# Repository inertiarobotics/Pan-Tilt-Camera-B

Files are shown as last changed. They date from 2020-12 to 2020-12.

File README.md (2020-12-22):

# Pan Tilt Mechanism - Version B
A lightweight and a less bulkier version of [Pan Tilt Camera A](https://github.com/inertiarobotics/Pan-Tilt-Camera-A)

For Raspberry Pi Camera V2.

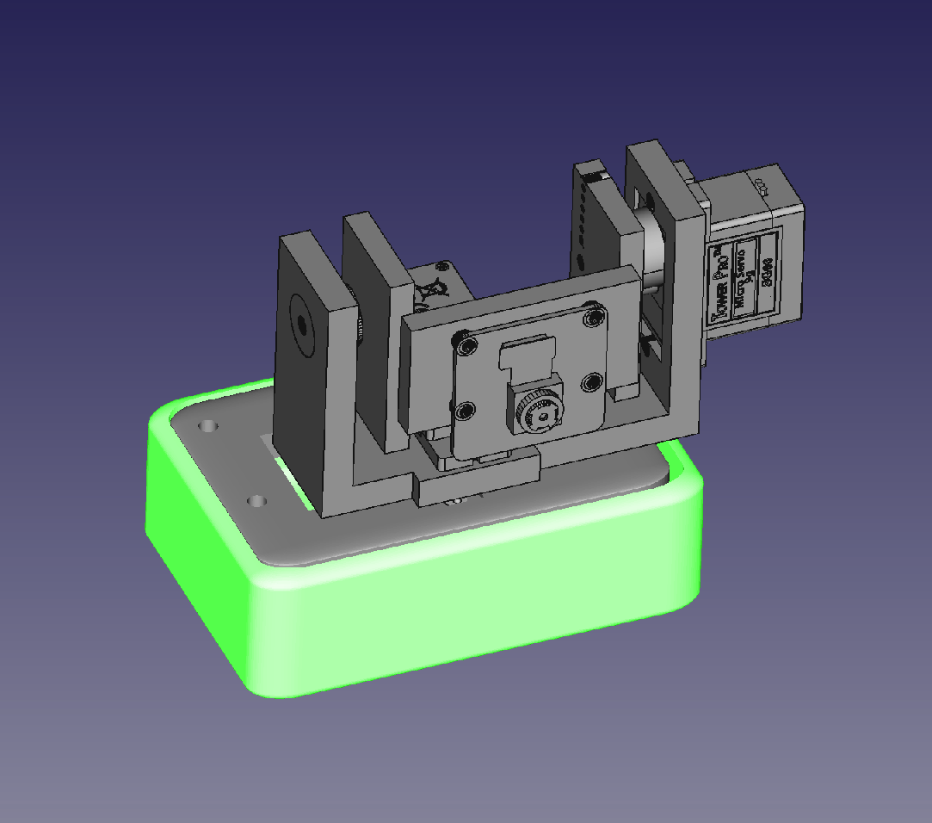
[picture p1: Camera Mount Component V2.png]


# Why ? 
The [version A](https://github.com/inertiarobotics/Pan-Tilt-Camera-A), which is a predecessor of Pan-Tilt-Camera-B was more bulky and is meant to be used for achieve more stability.

# Why we built [Version A](https://github.com/inertiarobotics/Pan-Tilt-Camera-A) ?
The widely available pan tilt mechanism kits sold by adafruit, sparkfun or piromoni (https://www.sparkfun.com/products/14391) are quite cheap and handy to setup - which is great, but lack to offer stability, when the weight of the camera is raised due to additional lense attachments. The servo necks rattles and wiggles under motion. This design uses bearings at pan and tilt positions to offer a stabler design. The 1" bearing at the pan level secures the pan servo neck in place and prevents vertical jerky motions - suitable for robotic applications, RC cars, boars , airplanes

## Prerequisites / BOM:
- 2 units of SG 90 - Micro 9g servos - one for pan and other for tilt.
- 4 units of 673ZZ bearings ( 3x6x2.5 )  - Outer diamer 6mm, Inner diameter 3mm, height 2.5mm 
(https://www.amazon.com/10-Bearing-6700ZZ-10x15x4-Shielded/dp/B002BBK5MY)
- #2-56 x 1/2“ machine screws - 10 units
- Glue
- 3D printed parts:
  - Camera Mount Component V2 - Tilt Holder
  - Camera Mount Component V2 - PCB Holder
  - Camera Mount Component V2 - Base Holder
  - Camera Mount Component V2 - Pan Holder
- Raspberry Pi Camera V2

## Assembly Guide:

See the Install Instructions - Pan Tilt Camera B.pdf file at 

https://github.com/inertiarobotics/Pan-Tilt-Camera-B/blob/main/Install%20Instructions%20-%20Pan%20Tilt%20Camera%20B.pdf

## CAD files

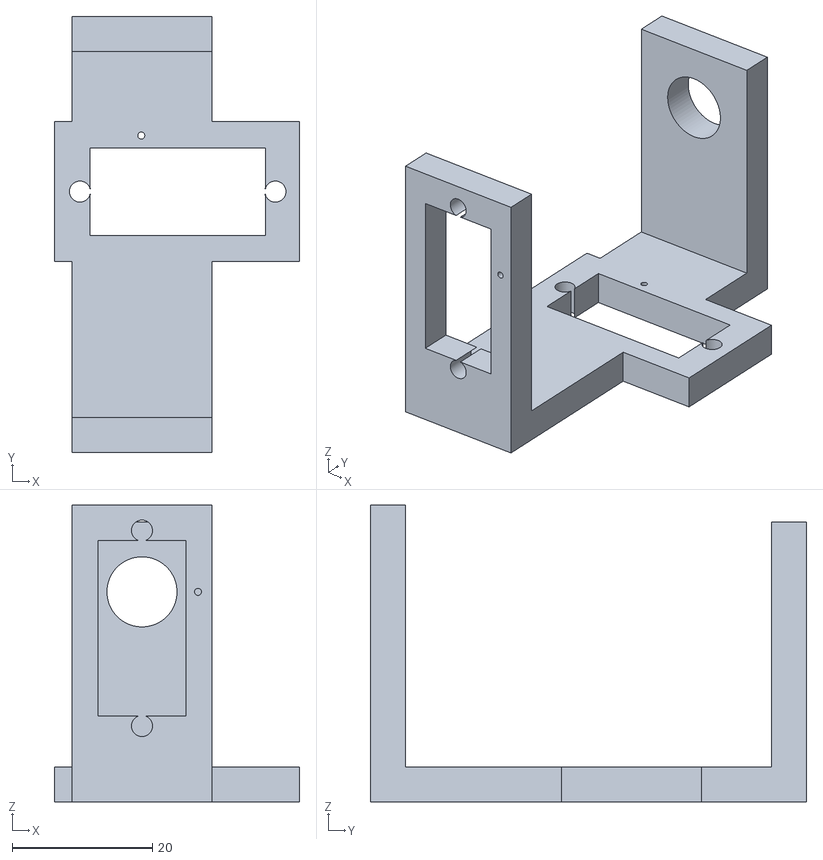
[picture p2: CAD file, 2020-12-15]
Camera Mount Component V2 - Tilt Holder.stl
35.0 x 62.2 x 42.4

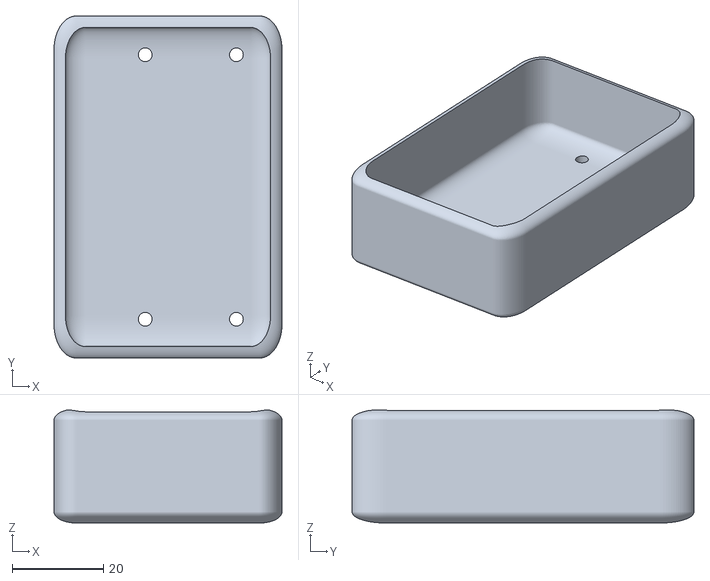
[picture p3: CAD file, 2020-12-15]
Camera Mount Component V2 - Base Holder.stl
50.0 x 75.0 x 24.8

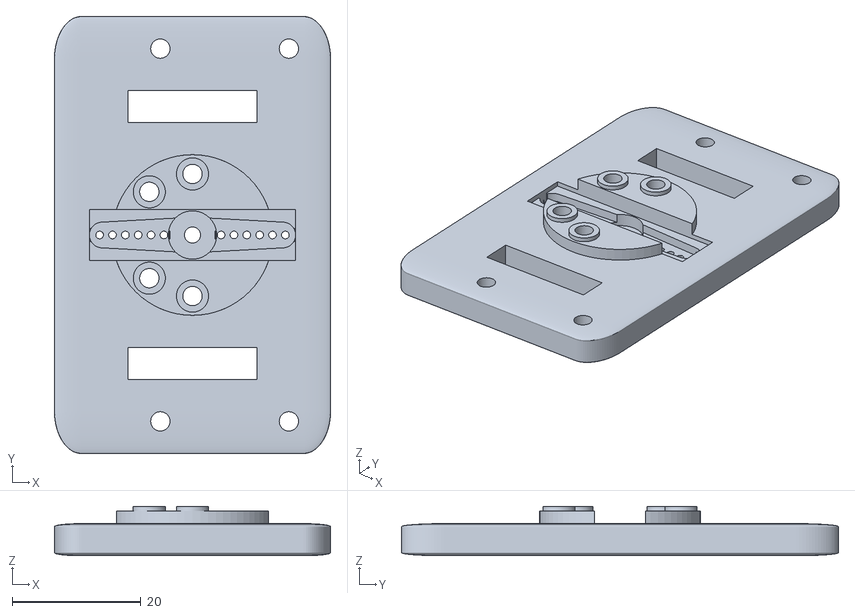
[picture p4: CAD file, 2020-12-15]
Camera Mount Component V2 - Pan Holder.stl
43.0 x 68.0 x 7.70

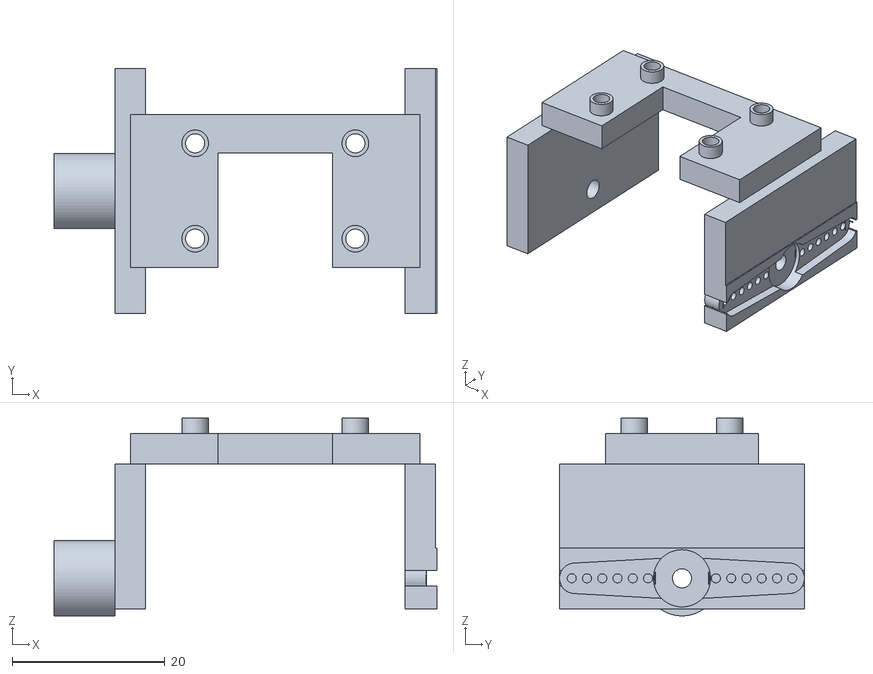
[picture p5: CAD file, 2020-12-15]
Camera Mount Component V2 - PCB Holder.stl
50.2 x 32.1 x 25.9

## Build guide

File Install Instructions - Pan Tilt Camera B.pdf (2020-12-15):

Step 1:
Insert the Camera Mount Component V2 - PCB Holder.stl into the Camera Mount Component V2 - Tilt Holder.stl

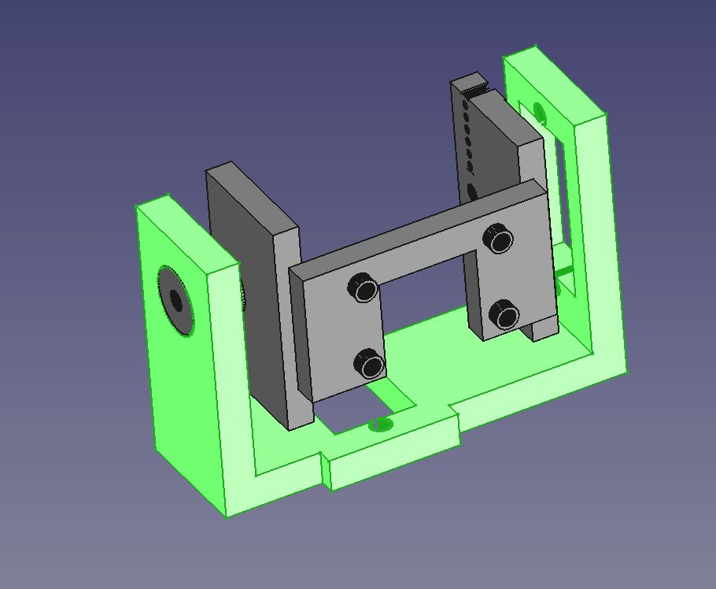
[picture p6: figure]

Step 2: Affix the tilt servo horn into the Camera Mount Component V2 - PCB Holder.stl with glue.

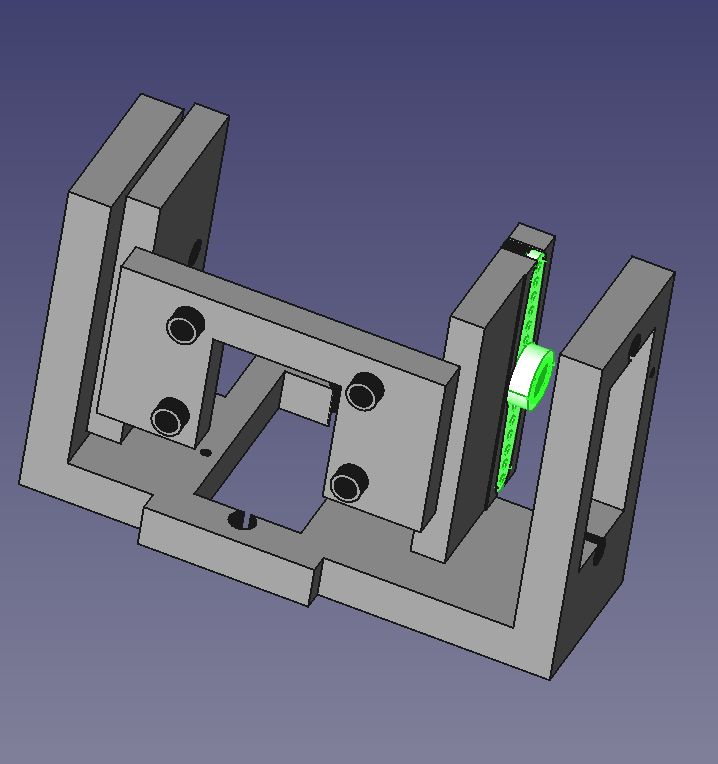
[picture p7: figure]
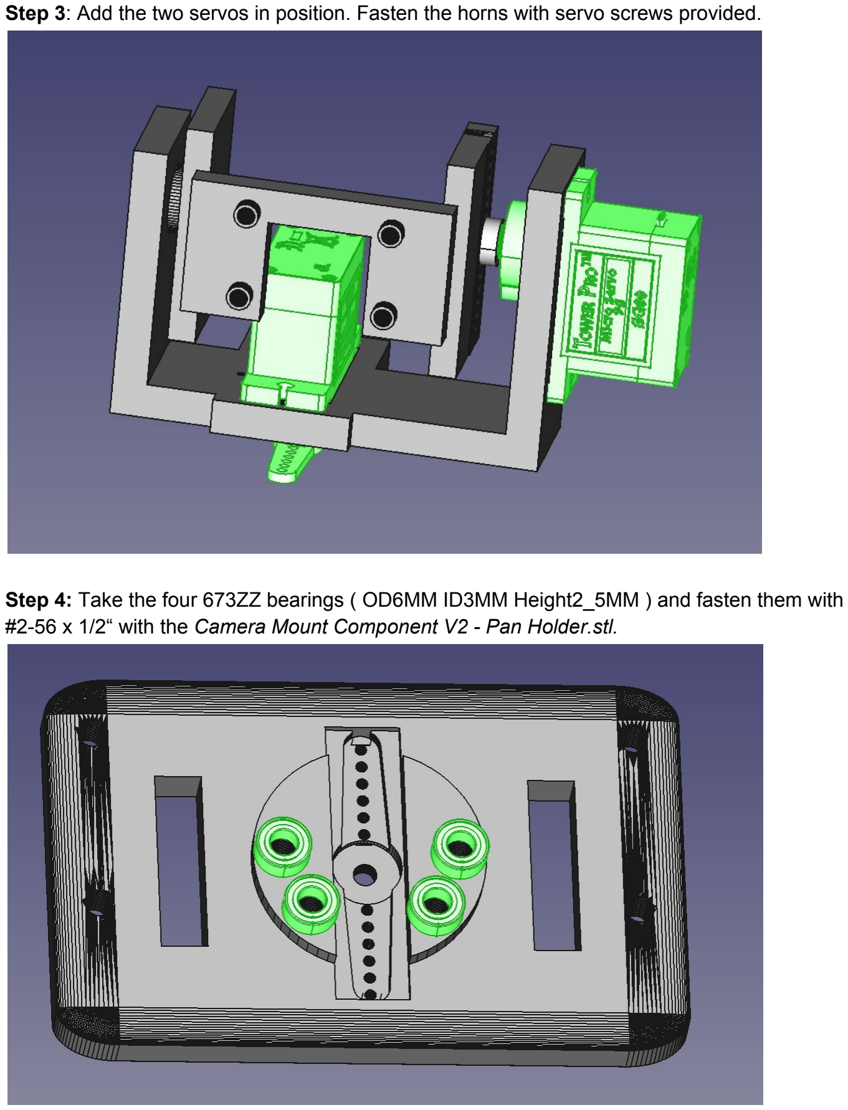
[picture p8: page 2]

Step 3: Add the two servos in position. Fasten the horns with servo screws provided.
Step 4: Take the four 673ZZ bearings ( OD6MM ID3MM Height2_5MM ) and fasten them with #2-56 x 1/2“ with the Camera Mount Component V2 - Pan Holder.stl.

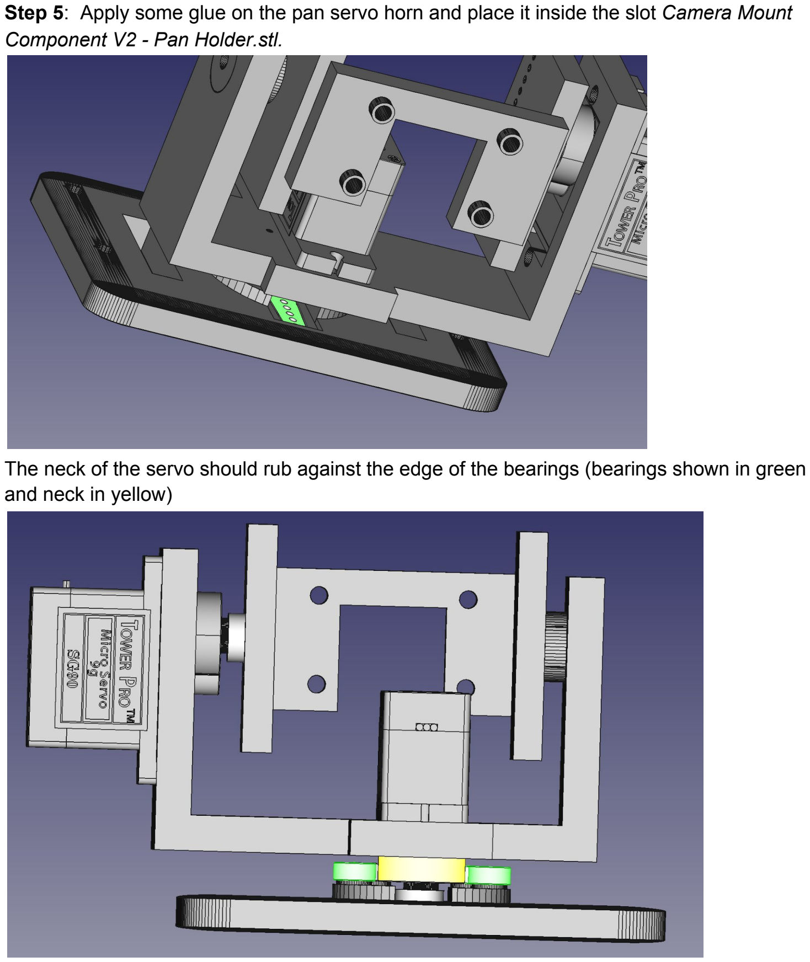
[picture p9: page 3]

Step 5: Apply some glue on the pan servo horn and place it inside the slot Camera Mount Component V2 - Pan Holder.stl.

The neck of the servo should rub against the edge of the bearings (bearings shown in green and neck in yellow)

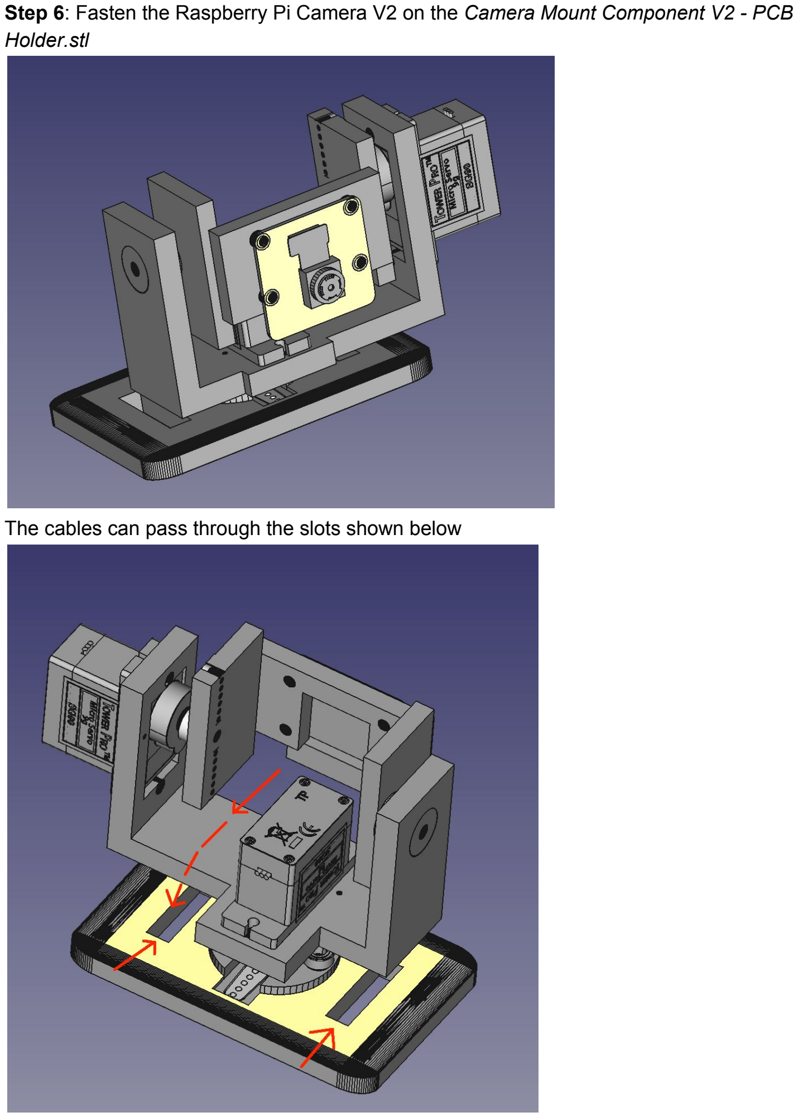
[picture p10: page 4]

Step 6: Fasten the Raspberry Pi Camera V2 on the Camera Mount Component V2 - PCB Holder.stl

The cables can pass through the slots shown below

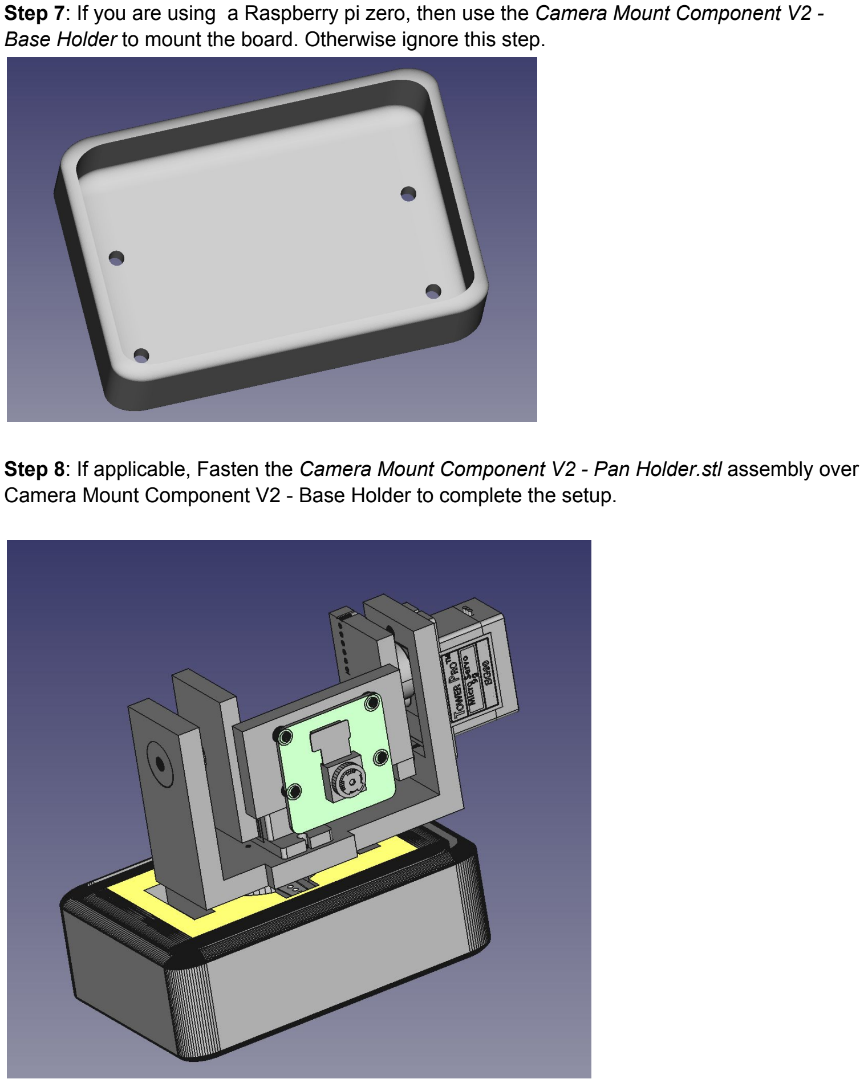
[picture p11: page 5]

Step 7: If you are using a Raspberry pi zero, then use the Camera Mount Component V2 -Base Holder to mount the board. Otherwise ignore this step.
Step 8: If applicable, Fasten the Camera Mount Component V2 - Pan Holder.stl assembly over Camera Mount Component V2 - Base Holder to complete the setup.
